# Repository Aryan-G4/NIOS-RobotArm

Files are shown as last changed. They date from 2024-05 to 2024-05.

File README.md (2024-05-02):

# NIOS-RobotArm
A 3DoF Robot Manipulator programmed and controlled using a DE1-SoC's embedded NIOS II processor. Fully designed in-house.

Funded by the University of Toronto

Sponsored by StepperOnline

Aryan Ghosh | David Xu

[Project Demo:](https://youtu.be/5mW0npLePgE)

## Introduction 
The first of its kind, the NIOS-Robot arm is a robot completely designed in-house and controlled by an FPGA.
It boasts a fully 3D-printed body, NEMA17 stepper motors, a breadboarded electrical system, and a low-level embedded software system.
This project was created to gain experience designing dynamic mechanical systems, conduct dyanamic and force analysis and configure and drive motors. 



Today, robot manipulators are used worldwide to weld, assemble, transport, package, pick, and place. Seeing the importance of these concepts, we decided to create a simplified, scaled-down, cost-effective version of these industrial robots.




*These graphics are for the previous Mk1*

## Key Features
* Free Movement in XYZ space
* Detachable and modular End-Effector
* Zero Backlash 5:1 Geared stepper motors
* Joint Rotation Limits in software
* Switch-controlled tactile User interface
* Solid Concrete Base
  
## Mechanical Design
 


The mechanical design of this system has been through several iterations, all developed in Solidworks. This was done because of Solidowork's Assembly environment, where it is extremely easy to create new parts within an assembly related to others. 

The stepper motor that we chose for the project has an extremely high quality and precise .STEP file, and we used this to create an extremely low tolerance gap between the motors and the body.
All three motors were securely fastened using M3 screws measured at the correct length to engage as many threads of the screw as possible for the most secure connection.



Transferring the output from the stepper motor shaft to a joint linkage was challenging. This was done by attaching an 8mm flange shaft coupler to the arm linkage. This was all held in place by four No.4 bolts and nuts. There was an issue with the nuts coming loose, and in the next revision, locknuts will be used.


Upon completing the structural and dynamic analysis of the robot and evaluating the torque produced by each motor, the length of both arm linkages was established. This was after several iterations.

Due to the need for transportation between the workshop and the lab, the robot could not be bolted down to a table to be held in place. To save costs and negate any moment produced by the linkages and end effectors, We poured concrete into the base of the robot, making it so heavy that any movement or forces applied to or by the robot would not cause it to fall over. 




## Embedded Software Design
The software takes the hardware provided to it (GPIO pins, Switches, and LEDs), and interprets the I/O to drive the motors. The software is designed to process only one instruction at a time. It works by polling all the switches waiting for any one to be switched. Once it detects that a switch has been flipped high, the program moves to a subroutine that detects which switch has been flipped, generates the appropriate GPIO pins to write to, and then generates a square wave to those pins. The program continues to generate this signal until the switch is flipped down. During this time, any other inputs and switch flips are completley ignored, allowing the user to focus on one joint at a time. 


Joint limits were implemented by creating variables that counted how many steps each motor took and calculating how many degrees the motor moved by. Assuming there are no missed steps, the software can detect when a motor has rotated 180 degrees, and it can prevent the square wave to the step pin from being generated.

All code can be found in **main.c**
## Electrical Design
The electrical design handles two power rails:  a 24V power line and a 5V logic line. Each nema17 stepper motor required approximately 12-24V of power at 2.2A to produce its advertised torque. This was all controlled through the A4988 Stepper motors. The A4988 offers 2 important logic pins, step and direction. Every time the step pin goes high (with a logic of 5V), the stepper motor rotates by 0.36 degrees. To allow for continuous rotation, we needed to generate a **square wave** to send to the driver, causing the motor to step so frequently, creating the illusion of seamless rotation. The rotation direction would depend on the direction pin, which causes the motor to rotate clockwise when low (~0V) and counterclockwise when high (~5V). The A4988 drivers had to be tuned to the right resistance, as too much current can fry the IC and too little current will not give us enough motor torque. 

Shown below is the electrical system:



The GPIO pins from the FPGA are shown on the left. The wires are in groups of two (step and direction) and connect to the step/dir pins of the a4988 Stepper motor drivers shown on the breadboard.on the right there are 3 groups of 4 wires(red,blue, black, green) These groups are for each stepper motor as each motor requires 4 wires. Additionally on the right there is a grey and purple wire. These to wires are connected to the right side power raila nd provide 24V to the system.

All wires are colour coded as black and red are often known to be power/ground. 
## Iterations
Our Mk1 iteration was extremely durable, but both arms were far too heavy. Linkages were unnecessarily large, and the 3d printed infill density was far too high. This caused the elbow motor (located above the base) to miss steps because it 



*Old mk1*
Here is a comparison between the old and new first linkage:



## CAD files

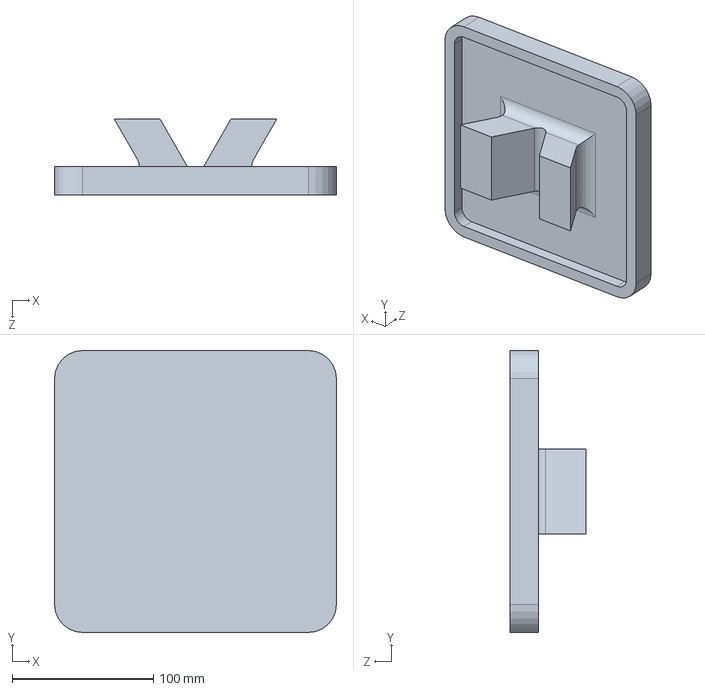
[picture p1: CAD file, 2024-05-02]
Solidworks/Base_cover.SLDPRT
200.0 x 200.0 x 53.7 mm

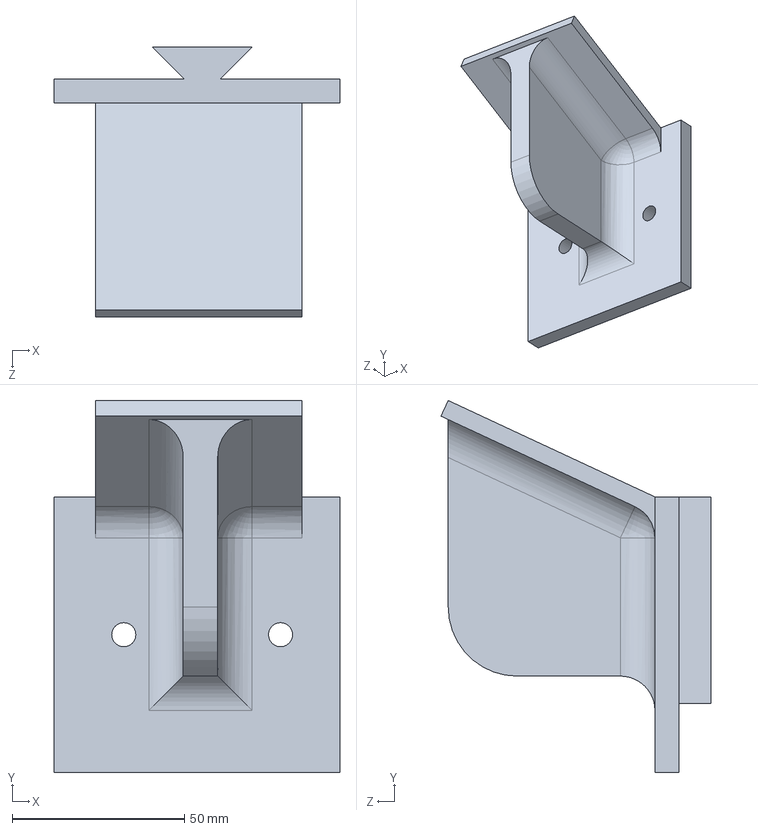
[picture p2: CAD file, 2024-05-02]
Solidworks/endpoint canvas.SLDPRT
83.0 x 108.0 x 78.4 mm

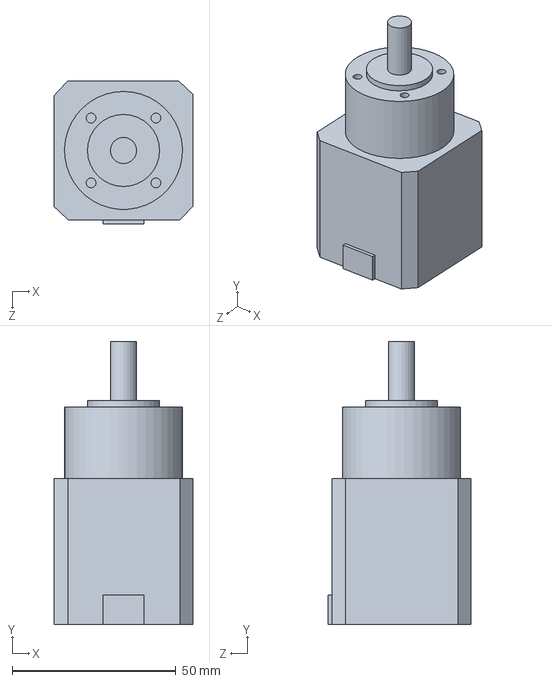
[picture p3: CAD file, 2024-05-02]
Solidworks/NEMA17-lowpoly.SLDPRT
42.3 x 86.4 x 43.6 mm

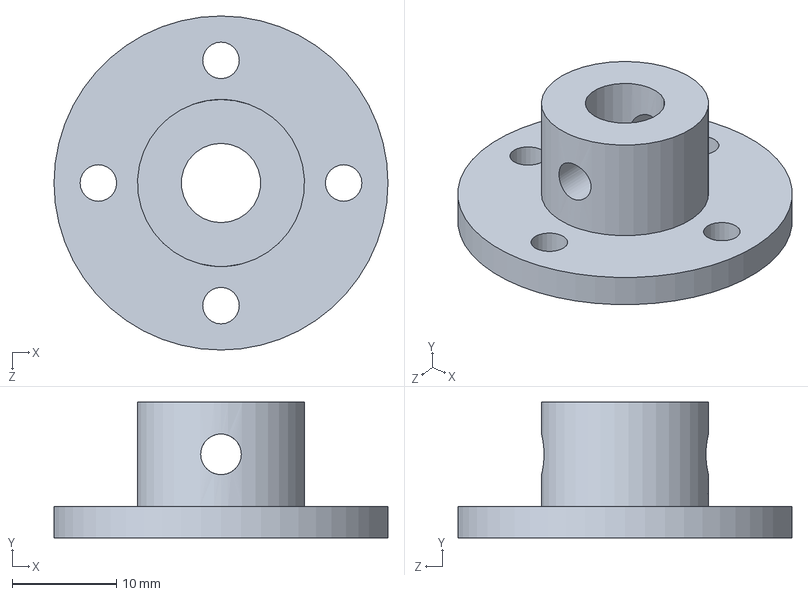
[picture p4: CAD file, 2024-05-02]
Solidworks/flange_coupling_8mmdia_v2.SLDPRT
32.0 x 13.0 x 32.0 mm

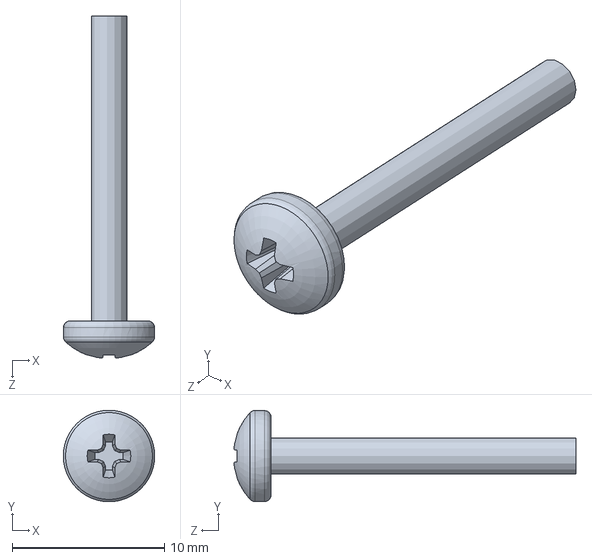
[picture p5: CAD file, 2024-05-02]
Solidworks/90116A165_316 Stainless Steel Pan Head Phillips Screws.SLDPRT
6.00 x 6.00 x 22.4 mm

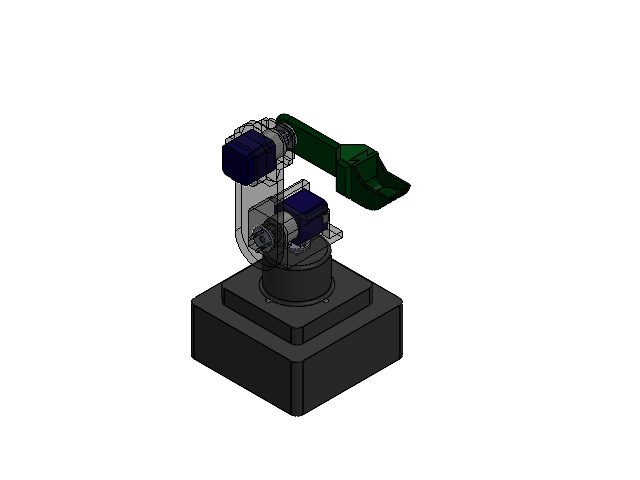
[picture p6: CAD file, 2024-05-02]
Solidworks/MASTER_ASSEMBLY_MK1.5.SLDASM
Part2^MASTERASSEMBLYV3
NEMA17-lowpoly x 3
Part3^MASTERASSEMBLYV3
flange_coupling_8mmdia_v2 x 3
Part4^MASTERASSEMBLYV3
Part6^MASTERASSEMBLYV3
Part8^MASTERASSEMBLYV3
Part9^MASTERASSEMBLYV3
Part10^MASTERASSEMBLYV3
90116A165_316 Stainless Steel Pan Head Phillips Screws x 4

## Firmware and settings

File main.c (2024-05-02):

  //CREATED BY DAVID XU AND ARYAN GHOSH FOR THE NIOS II ROBOT//
  
  #include <math.h>
  #include <stdbool.h>
  #include <stdio.h>
  //Defining I/O addresses for NIOSII GPIO
  #define ADDR_JP1PORT ((volatile char *) 0xFF200060)
  #define ADDR_JP2PORT ((volatile char *) 0xFF200070)
  //Onboard Hardware initialization
  #define LED ((volatile long *) 0xFF200000)
  #define PUSHBUTTONS ((volatile long *) 0xFF200050)
  #define SWITCHES ((volatile long *) 0xFF200040)
  // PS/2 port address
  #define PS2_ptr ((volatile int *) 0xFF200100)
  #define PUSHBUTTONS ((volatile long *) 0xFF200050)

  #define NUM_JOINTS 3
  //Motor set to microstepping
  //1.8 degrees /5 due to 5:1 planetary gear ratio and /4 due to quarter step a4988 driver setting
  double STEP_SIZE = 1.8/20;
  // forward kinematics
  typedef struct {
      double x;
      double y;
      double z;
  } Vector3D;

  typedef struct {
      double theta;
      double length;
      double upperlimit, lowerlimit;
  } Joint;

  typedef struct {
      Joint joints[NUM_JOINTS];
  } RoboticArm;

  void write_pixel(int x, int y, short colour) {
    volatile short *vga_addr=(volatile short*)(0x08000000 + (y<<10) + (x<<1));
    *vga_addr=colour;
  }

  /* use write_pixel to set entire screen to black (does not clear the character buffer) */
  void clear_screen() {
    int x, y;
    for (x = 0; x < 320; x++) {
      for (y = 0; y < 240; y++) {
      write_pixel(x,y,0);
    }
    }
  }

  void background() {
    int x, y;
    for (x = 0; x < 320; x++) {
      for (y = 0; y < 240; y++) {
        if(y < 179){
          write_pixel(x,y,image[y][x]);
        }else{
          write_pixel(x,y,0);
        }
    }
    }
  }

  /* write a single character to the character buffer at x,y
   * x in [0,79], y in [0,59]
   */
  void write_char(int x, int y, char c) {
    // VGA character buffer
    volatile char * character_buffer = (char *) (0x09000000 + (y<<7) + x);
    *character_buffer = c;
  }

bool isValidPosition(double theta1, double theta2, double theta3) {
    // Define the rotational limits for each motor
    const double motor1_min = -180.0;
    const double motor1_max = 180.0; // 360 degrees in radians

    const double motor2_min = 85;
    const double motor2_max = 95; // 200 degrees in radians

    const double motor3_min = -135.0;
    const double motor3_max = +135.0; // 270 degrees in radians

    // Check if the position is within the limits for each motor
    if (theta1 < motor1_min || theta1 > motor1_max)
        return false;
    if (theta2 < motor2_min || theta2 > motor2_max)
        return false;
    if (theta3 < motor3_min || theta3 > motor3_max)
        return false;

    // If all checks pass, the position is valid
    return true;
}

Vector3D cylindricalToCartesian(double theta, double radius, double height) {
    Vector3D cartesian;
    cartesian.x = radius * cos(theta);
    cartesian.y = radius * sin(theta);
    cartesian.z = height;
    return cartesian;
}


void motor(int sw, RoboticArm *arm){
  long count = 2500;
  int i = 0;
  int led = inttohex(sw);
  int index = (int)(sw/2);
  //long PBreleases;
  long Swval = *SWITCHES;

  while(Swval != 0){
    Swval = *SWITCHES;
    if(i == 0){
      if(sw % 2 == 1){
        led = led ^ inttohex(sw-1);  //xor for toggling led
        
        if((led & inttohex(sw-1)) != 0){
          arm->joints[index].theta += STEP_SIZE;
          if(arm->joints[index].theta >= arm->joints[index].upperlimit){ break;}
        }
      } else {
        led = led ^ inttohex(sw);  //xor for toggling led
        if(led != 0){
          arm->joints[index].theta -= STEP_SIZE;
          if(arm->joints[index].theta <= arm->joints[index].lowerlimit){ break;}
        }
      }
      i = count;
    }else{
       i--;
    }

    *ADDR_JP1PORT = led;
    *LED = led;

  }
  *LED = 0;
  *ADDR_JP1PORT = 0;
  return;
}


void moveMotor(Joint* vector, double targetAngle, int num) {
    // Determine the direction of rotation
    bool clockwise = (vector->theta > targetAngle);
    long count = 5000;
    int i = 0;
    int led = inttohex(num*2);
    // Move the motor until it reaches the target angle
    do {
    if(i == 0){
      if (clockwise){
        led = led ^ inttohex(num*2+1);  //xor for toggling led
        i = count;
        if((led & inttohex(num-1)) != 0){
          vector->theta += STEP_SIZE;
        }
      }else{
        led = led ^ inttohex(num*2);  //xor for toggling led
        i = count;
        if(led != 0){
          vector->theta -= STEP_SIZE;
        }
      }

    }else{
       i--;
    }

    *ADDR_JP1PORT = led;
    *LED = led;

  }while((int)vector->theta != (int)targetAngle && vector->theta > vector->lowerlimit && vector->theta < vector->upperlimit && *SWITCHES != 0);
  *LED = 0;
  *ADDR_JP1PORT = 0;
}


void moveArmToCoordinates(RoboticArm *arm, double theta, double radius, double height) {
  Vector3D targetPosition = cylindricalToCartesian(theta, radius, height);

  double L1 = arm->joints[0].length;
  double L2 = arm->joints[1].length;
  double L3 = arm->joints[2].length;

  double x = targetPosition.x;
  double y = targetPosition.y;
  double z = targetPosition.z;

  // Calculate theta1
  //arm->joints[0].theta = atan2(y, x);
  moveMotor(&arm->joints[0], atan2(y, x), 0);
  // Calculate theta2
  double D = (x * x + y * y + (z - L1) * (z - L1) - L2 * L2 - L3 * L3) / (2 * L2 * L3);
  //arm->joints[2].theta = atan2(-sqrt(1 - D * D), D);
  moveMotor(&arm->joints[2], atan2(-sqrt(1 - D * D), D), 2);

  double c1 = cos(arm->joints[0].theta);
  double s1 = sin(arm->joints[0].theta);
  double c3 = cos(arm->joints[2].theta);
  double s3 = sin(arm->joints[2].theta);

  double A = L2 + L3 * c3;
  double B = L3 * s3;
  double C = z - L1;
  double theta2_1 = atan2(C, sqrt(x * x + y * y)) - atan2(B, A);
  double theta2_2 = atan2(C, -sqrt(x * x + y * y)) - atan2(B, A);

  // Choose the solution closest to the previous angle to avoid joint flips
  if (fabs(theta2_1 - arm->joints[1].theta) < fabs(theta2_2 - arm->joints[1].theta))
    moveMotor(&arm->joints[1], theta2_1, 1);
  else
    moveMotor(&arm->joints[1], theta2_2, 1);
}

  int main () {
     //init interface directions
     *(ADDR_JP2PORT+4) = 0xffffffff; //set every JP2 bit direction to output
     *(ADDR_JP1PORT+4) = 0xffffffff; //set every JP1 bit dir to output

    clear_screen();
    background();


    int x = 0;
    int y = 50;
    char* hw;
    unsigned char byte1 = 0;
    unsigned char byte2 = 0;
    unsigned char byte3 = 0;


    long PBval;
    int checkswitch;
    int sw;
    int PS2_data, RVALID;
    bool turned = false;
    RoboticArm arm;

    // Initialize arm parameters
    arm.joints[0].length = 0;
    arm.joints[0].theta = 0;
    arm.joints[0].upperlimit = 180;
    arm.joints[0].lowerlimit = -180;

    arm.joints[1].length = 225;
    arm.joints[1].theta = 90;
    arm.joints[1].upperlimit = 95;
    arm.joints[1].lowerlimit = 85;

    arm.joints[2].length = 150;
    arm.joints[2].theta = 0;
    arm.joints[2].upperlimit = 135;
    arm.joints[2].lowerlimit = -135;

    while(1){
      int checkswitch = *(SWITCHES);
      if(checkswitch  == 0b1000000){
        moveArmToCoordinates(&arm, 0.0, 0.0, 300.0);
        moveArmToCoordinates(&arm, 0.0, 0.0, 375.0);
      }

      if (checkswitch != 0){
        if(!turned){
          sw = hextoint(checkswitch);
          motor(sw, &arm);
          turned = true;
        }else{
          sw = 0;
        }
      }else{
        turned = false;
      }

    }
     return 0;
  }

int motornumber(int sw){
  if(sw == 0 || sw ==1){
    return 1;
  }
  if (sw == 2  || sw ==3){
    return 2;
  }
  if (sw == 4 || sw ==5){
    return 3;
  }
}

int inttohex(int sw){
  if(sw == 0){
    return 0b1;
  }
  if(sw == 1){
    return 0b10;
  }
  if(sw == 2){
    return 0b100;
  }
  if(sw == 3){
    return 0b1000;
  }
  if(sw == 4){
    return 0b10000;
  }
  if(sw == 5){
    return 0b100000;
  }
}

int hextoint(int checkswitch){
  if(checkswitch == 0b1){
    return 0;
  }
  if(checkswitch == 0b10){
    return 1;
  }
  if(checkswitch == 0b100){
    return 2;
  }
  if (checkswitch == 0b1000){
    return 3;
  }
  if (checkswitch == 0b10000){
    return 4;
  }
  if (checkswitch == 0b100000){
    return 5;
  }
}

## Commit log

2024-05-02 uploaded mk1.5 masterassembly
    [MASTER_ASSEMBLY_MK1.5.SLDASM]
2024-05-02 Added non-virtual components
    [90116A165_316 Stainless Steel Pan Head Phillips Screws.SLDPRT, Base_cover.SLDPRT, NEMA17-lowpoly.SLDPRT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]
